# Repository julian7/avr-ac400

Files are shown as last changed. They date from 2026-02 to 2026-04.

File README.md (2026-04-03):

# Record Power AC400 controller

This repository contains a drop-in replacement PCB and firmware for the [Record Power AC400 Air Filter controller](https://www.recordpower.co.uk/product/two-stage-air-filter-with-remote-3-speeds-and-time-delay).

The original AC400 controller is prone to failure due to its simplistic power supply design, which often results in various failures. While the company's support is very good, the replacement controller is still prone to the same issues.

This design aims to provide a solution that is more robust, and tries to keep using original parts where possible. It also uses an ~~ATmega88PA~~ ATmega328P microcontroller, as existing refurbishment stock (note: the ATmega88 I had probably has SPIEN fuse unprogrammed, so I couldn't flash it at the end). The PCB and firmware is compatible with the whole line of ATmega48P/88P/168PA/328P line though.

## Case design

The board PCB is designed to fit into the original AC400 electronics enclosure, but there is a different LED divider grill design, which is 3D printed. The 3D model and the FreeCAD source are available in the `mechanical` directory, and it can be printed with a 3D printer.

The 3D design and model for the case is also provided, to allow further modifications.

## PCB design

The PCB is designed using KiCad 10, and is available in the `hardware` directory. The form factor is designed to fit into the original AC400 enclosure, and it uses the same connectors for the fan and power supply. It relies of the Alternative Kicad Library plugin for resistor footprints. Interactive BOM is generated using the [Interactive Html Bom](Github: https://github.com/openscopeproject/InteractiveHtmlBom) plugin, and gerber file packages are generated using the [gerber to order](https://github.com/asukiaaa/gerber_to_order) plugin.

## Firmware

The firmware is written in C using AVR-GCC toolchain, and it is available in the `firmware` directory. It is based on the original firmware functionality, with some improvements and bug fixes.

## Flashing the firmware

To flash the firmware onto the microcontroller, you will need an AVR programmer (e.g., USBasp, [ATMEL-ICE](https://www.microchip.com/en-us/development-tool/atatmel-ice)) and AVRDUDE software.

## Measurement points and troubleshooting

The PCB includes test points for measuring various signals:

- TP1: 3.3V power supply
- TP2: Ground
- TP3: Low speed mosfet drain
- TP4: Low speed mosfet gate
- TP5: Mid speed mosfet drain
- TP6: Mid speed mosfet gate
- TP7: High speed mosfet drain
- TP8: High speed mosfet gate

When troubleshooting, supply 3.3V power to the PCB through J8, so that 230V is not present on the board.

J1 is providing standard ISP connectivity. Manual reset can be performed by shorting JP1 (also labeled "RESET").

## Wiring and functions

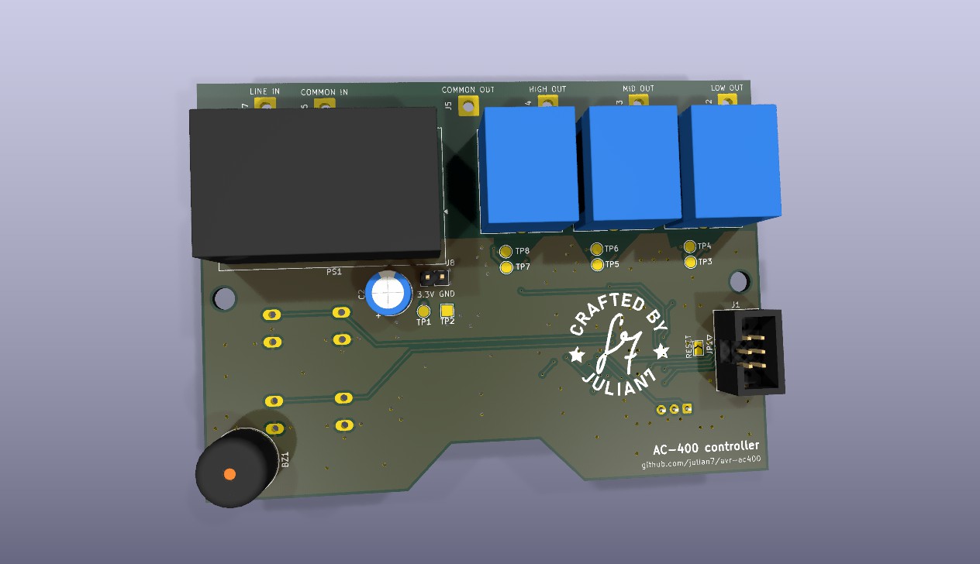
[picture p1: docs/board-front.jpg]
Board front


When assembled into the original AC400 enclosure, the PCB will be connected to the following components:

- LINE IN: 230V AC input
- COMMON IN: Common line for the fan and the power supply
- COMMON OUT: White wire to the fan
- LOW OUT: Blue (or brown) wire to the fan
- MID OUT: Black wire to the fan
- HIGH OUT: Red wire to the fan

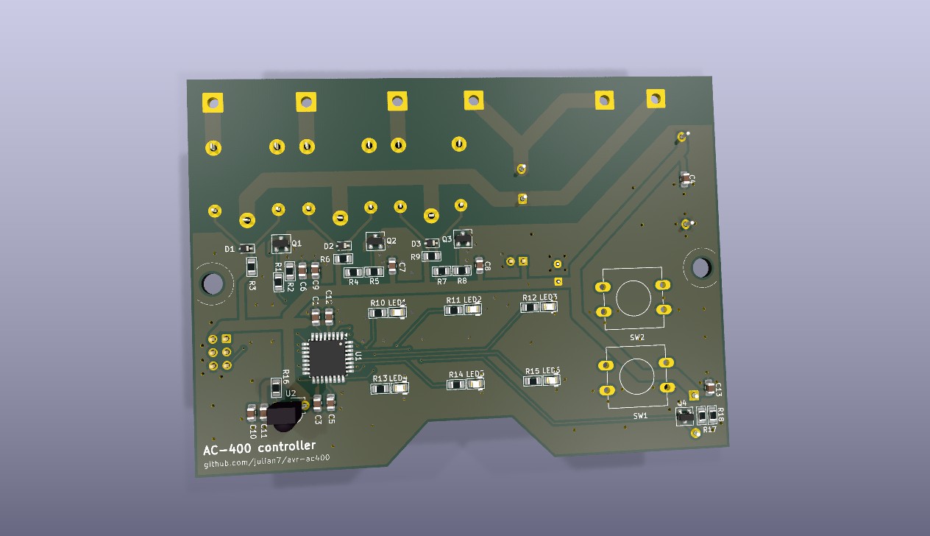
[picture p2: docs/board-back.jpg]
Board back


LED functions:

- LED1: Timer for 1 hour
- LED2: Timer for 2 hours
- LED3: Timer for 4 hours
- LED4: High speed indicator
- LED5: Medium speed indicator
- LED6: Low speed indicator

Button functions:

- SW1: On/Speed (cycles through Off, Low, Mid, High)
- SW2: Off

Infrared remote control functions:

- Red: Off
- Green: On/Speed
- Yellow: Timer (cycles through Off, 1 hour, 2 hours, 4 hours)

Buzzer signals:

- Short beep: Button press / infrared button feedback
- Long beep: Timer end
- Long beep with 1/2/4 short beeps: timer set to 1/2/4 hours
- Two long beeps: Off

## Build experience

Building this project was quite an experience. First off, soldering the MCU was not much of a challenge, and I felt like I could handle 0603 package size too, or even 0402 if the space is tight. I would use an ESP32-C3 board if I were to do it again: that would make it remote controllable.

Originally, I wanted to use an old ATmega88PA, but I couldn't even read its fuses. So that I ordered a few ATmega328P, which are pin-compatible. Fortunately, because I could made one of them a short circuit. It would've been nicer if the design accepted ATmega328PB, but I just didn't want to risk cutting wires at that point.

I almost fried my Raspberry Pi4 while writing the firmware, so buying a very cheap USBASP now feels like a no brainer. It's also not that bad if you don't screw up the ISP pinout. Fortunately, I could patch it up with bodge wires. Also, there was a nasty case of weird behavior and browning out, but as it turns out that was just microzig acting up. Switching back to avr-libc made the issue go away.

The original plan was to reuse the original case and the 12mm TACT switches, but I mistakenly ordered an earlier version of the PCB, where mounting holes have been placed closer together so I ended up 3D printing my own case. Later on, I even managed to break off the buttons as I tried to assemble it back together, and I only had 6x6mm switches so I ended up propping up some button spacers to be able to operate the device.

All in all, I'm very happy about the outcome.  Obviously it could've been much better, but this is still well beyond my expectations.

## Similar projects

- [AC400Controller](https://github.com/thikone/AC400Controller): drop-in replacement PCB, firmware, and 3D printed enclosure. It uses Arduino Nano as the controller.

## License

This project is licensed under the Creative Commons Attribution 4.0 International License. See the [LICENSE](./LICENSE.md) file for details.

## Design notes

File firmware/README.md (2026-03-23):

# Firmware for the AC400 controller

## Install toolchain

- Install [just](https://github.com/casey/just/releases)
- Install the [AVR Libc](https://avrdudes.github.io/avr-libc/) toolchain. For exmple, on Debian / Ubuntu:

```shell
sudo apt update
sudo apt install -y gcc-avr binutils-avr avr-libc avrdude
```

On MacOS, you can use Homebrew:

```shell
brew install avr-gcc avrdude
```

## Build and flash

Run

```shell
make
just flash
```

The flash utility is taking a few parameters to specify your environment. The default values are for a Raspberry Pi using SPI0 from its GPIO, but you can override them with environment variables. For example:

- AVR_PROGRAMMER: The programmer to use with `avrdude`. Default is `usbasp-clone`.
- AVR_PART: The AVR part number to flash. Default is `m328p`.
- AVR_PORT: The port to use for flashing. Default is empty.
- AVR_FREQ: The frequency for flashing. Default is empty.
- TARGET: The target to flash. Default is `ac400`. This will flash `ac400.hex`.

Run `sudo -E just flash` if you need root permissions to access the SPI device. You can also set up udev rules to allow non-root access to the SPI device.

Please note: `-E` is used to preserve the environment variables when running `just` with `sudo`.

## Setting Fuses

Sometimes, you may need to set the fuses on the AVR microcontroller to configure its behavior. Setting and reading fuses are easy with just recipes:

```shell
just read-fuses
```

```shell
just set-fuses [-l 0xLF] [-h 0xHF] [-e 0xEF]
```

Where:
- `-l`: Set the low fuse byte (default: 0xe2).
- `-h`: Set the high fuse byte (default: 0xdf).
- `-e`: Set the extended fuse byte (default: 0xff).

## Default fuse settings

- LFUSE: establish clock source (CKDIV8 = 1, CKOUT = 1, SUT = 10, CKSEL = 0010). To measure clock, set CKOUT fuse (so that LFUSE should be 0xa2).
- HFUSE: RSTDISBL = 1, DWEN = 1, SPIEN = 0, WDTON = 1, EESAVE = 1, BOOTSZ = 11, BOOTRST = 1
- EFUSE: BODLEVEL = 111 (Brown-out detection disabled)

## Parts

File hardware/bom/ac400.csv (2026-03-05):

Reference | Qty | Value | DNP | Exclude from BOM | Exclude from Board | Footprint | Datasheet | Manufacturer | Distributor Link 1 | Distributor Link 2 | Distributor Link 3
BZ1 | 1 | Buzzer |  |  |  | Buzzer_Beeper:Buzzer_12x9.5RM7.6 | ~
C1,C3,C5,C6,C7,C8,C10,C12,C13 | 9 | 100n |  |  |  | Capacitor_SMD:C_0805_2012Metric_Pad1.18x1.45mm_HandSolder | ~
C2 | 1 | 470u |  |  |  | Capacitor_THT:CP_Radial_D8.0mm_P3.50mm | ~
C4,C9,C11 | 3 | 10u |  |  |  | Capacitor_SMD:C_0805_2012Metric_Pad1.18x1.45mm_HandSolder | ~
D1,D2,D3 | 3 | 1N4007 |  |  |  | Diode_SMD:D_SOD-323 | https://www.tme.eu/Document/5f8ffc5ac30fc86bac97d66040bf5502/1n400x.pdf
J1 | 1 | AVR-ISP-10 |  |  |  | Connector_IDC:IDC-Header_2x05_P2.54mm_Vertical | ~
J2 | 1 | LOW OUT |  | Excluded from BOM |  | Connector_Wire:SolderWire-1.5sqmm_1x01_D1.7mm_OD3.9mm | ~
J3 | 1 | MID OUT |  | Excluded from BOM |  | Connector_Wire:SolderWire-1.5sqmm_1x01_D1.7mm_OD3.9mm | ~
J4 | 1 | HIGH OUT |  | Excluded from BOM |  | Connector_Wire:SolderWire-1.5sqmm_1x01_D1.7mm_OD3.9mm | ~
J5 | 1 | COMMON OUT |  | Excluded from BOM |  | Connector_Wire:SolderWire-1.5sqmm_1x01_D1.7mm_OD3.9mm | ~
J6 | 1 | COMMON IN |  | Excluded from BOM |  | Connector_Wire:SolderWire-1.5sqmm_1x01_D1.7mm_OD3.9mm | ~
J7 | 1 | LINE IN |  | Excluded from BOM |  | Connector_Wire:SolderWire-1.5sqmm_1x01_D1.7mm_OD3.9mm | ~
J8 | 1 | 3.3V IN |  |  |  | Connector_PinHeader_2.54mm:PinHeader_1x02_P2.54mm_Vertical | ~
JP1 | 1 | Reset |  | Excluded from BOM |  | Jumper:SolderJumper-2_P1.3mm_Open_TrianglePad1.0x1.5mm | ~
K1,K2,K3 | 3 | SRD-03VDC-SL-C |  |  |  | Relay_THT:Relay_SPDT_SANYOU_SRD_Series_Form_C | http://www.sanyourelay.ca/public/products/pdf/SRD.pdf | Songle | https://www.hestore.hu/prod_10049169.html
LED1,LED2,LED3,LED4,LED5,LED6 | 6 | OF-SMD 2012 Green |  |  |  | PCM_LED_SMD_AKL:LED_0805_2012Metric | ~ | OPTOFLASH | https://www.hestore.hu/prod_10025832.html
PS1 | 1 | HLK-5M03 |  |  |  | Converter_ACDC:Converter_ACDC_Hi-Link_HLK-5Mxx | http://h.hlktech.com/download/ACDC%E7%94%B5%E6%BA%90%E6%A8%A1%E5%9D%975W%E7%B3%BB%E5%88%97/1/%E6%B5%B7%E5%87%8C%E7%A7%915W%E7%B3%BB%E5%88%97%E7%94%B5%E6%BA%90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
Q1,Q2,Q3,Q4 | 4 | IRLML2502 |  |  |  | PCM_Package_TO_SOT_SMD_AKL:SOT-23 | https://www.tme.eu/Document/48a23309a6589a98e2dca6345156a95a/IRLML2502TRPBF.pdf
R1,R4,R7,R17 | 4 | 100 |  |  |  | PCM_Resistor_SMD_AKL:R_0805_2012Metric_Pad1.15x1.40mm_HandSolder | ~
R2,R5,R8,R18 | 4 | 100k |  |  |  | PCM_Resistor_SMD_AKL:R_0805_2012Metric_Pad1.15x1.40mm_HandSolder | ~
R3,R6,R9 | 3 | 2.2 |  |  |  | PCM_Resistor_SMD_AKL:R_0805_2012Metric_Pad1.15x1.40mm_HandSolder | ~
R10,R11,R12,R13,R14,R15 | 6 | 120 |  |  |  | PCM_Resistor_SMD_AKL:R_0805_2012Metric_Pad1.15x1.40mm_HandSolder | ~
R16 | 1 | 10k |  |  |  | PCM_Resistor_SMD_AKL:R_0805_2012Metric_Pad1.15x1.40mm_HandSolder | ~
SW1 | 1 | ON |  |  |  | Button_Switch_THT:SW_PUSH-12mm | ~
SW2 | 1 | OFF |  |  |  | Button_Switch_THT:SW_PUSH-12mm | ~
SYM1 | 1 | Board footprint |  | Excluded from BOM |  | ac400:board_shape | ~
SYM2 | 1 | Julian7 logo |  | Excluded from BOM |  | ac400:julian7_makers_mark | ~
TP1 | 1 | 3.3V |  | Excluded from BOM |  | TestPoint:TestPoint_Pad_D2.0mm | ~
TP2 | 1 | GND |  | Excluded from BOM |  | TestPoint:TestPoint_Pad_2.0x2.0mm | ~
TP3 | 1 | LD |  | Excluded from BOM |  | TestPoint:TestPoint_Pad_D2.0mm | ~
TP4 | 1 | LG |  | Excluded from BOM |  | TestPoint:TestPoint_Pad_D2.0mm | ~
TP5 | 1 | MD |  | Excluded from BOM |  | TestPoint:TestPoint_Pad_D2.0mm | ~
TP6 | 1 | MG |  | Excluded from BOM |  | TestPoint:TestPoint_Pad_D2.0mm | ~
TP7 | 1 | HD |  | Excluded from BOM |  | TestPoint:TestPoint_Pad_D2.0mm | ~
TP8 | 1 | HG |  | Excluded from BOM |  | TestPoint:TestPoint_Pad_D2.0mm | ~
U1 | 1 | ATmega88PA-A |  |  |  | Package_QFP:TQFP-32_7x7mm_P0.8mm | https://www.microchip.com/en-us/product/ATmega88PA | Microchip Technology | https://www.digikey.hu/hu/products/detail/microchip-technology/ATMEGA88PA-AU/1886228 | https://hu.mouser.com/ProductDetail/Microchip-Technology/ATMEGA88PA-AU?qs=VXy%252BgAb0zZQ5AzLsp2xy0A%3D%3D | https://www.hestore.hu/prod_10029337.html
U2 | 1 | TSOP38238 |  |  |  | OptoDevice:Vishay_MINICAST-3Pin | http://www.vishay.com/docs/82491/tsop382.pdf

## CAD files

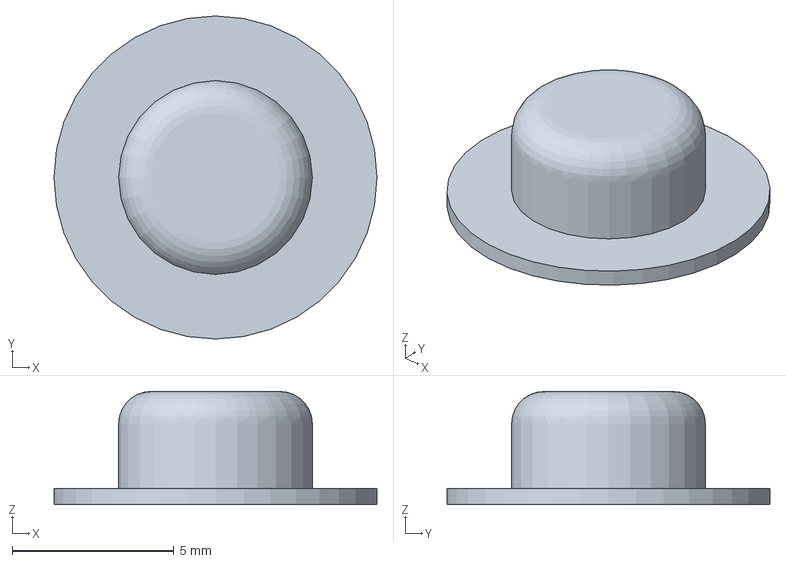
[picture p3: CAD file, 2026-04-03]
mechanical/ac400board-button.3mf
10.0 x 10.0 x 3.50 mm

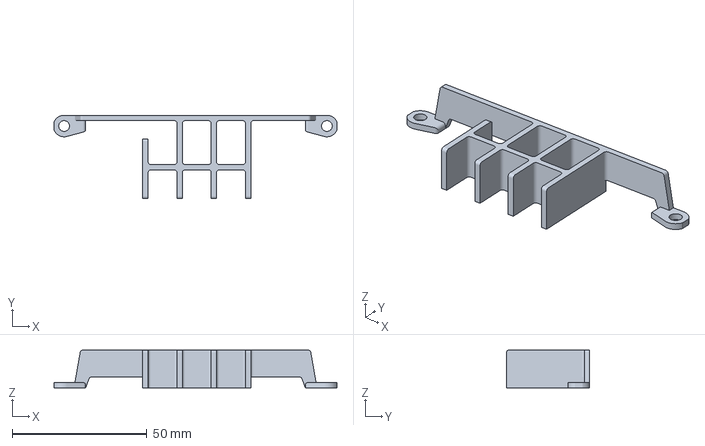
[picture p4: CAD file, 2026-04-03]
mechanical/ac400board-divider.3mf
105.0 x 31.0 x 14.0 mm

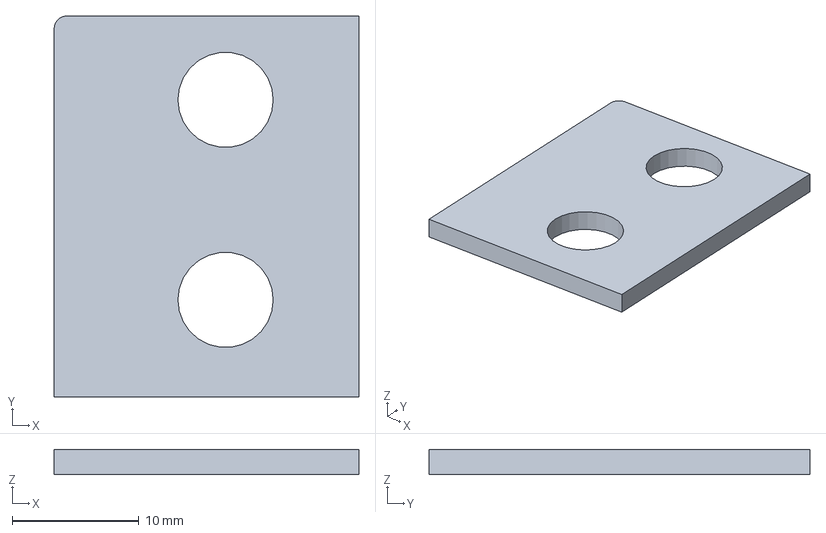
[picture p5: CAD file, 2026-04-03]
mechanical/ac400board-switch-stabilizer.3mf
24.0 x 30.0 x 2.00 mm

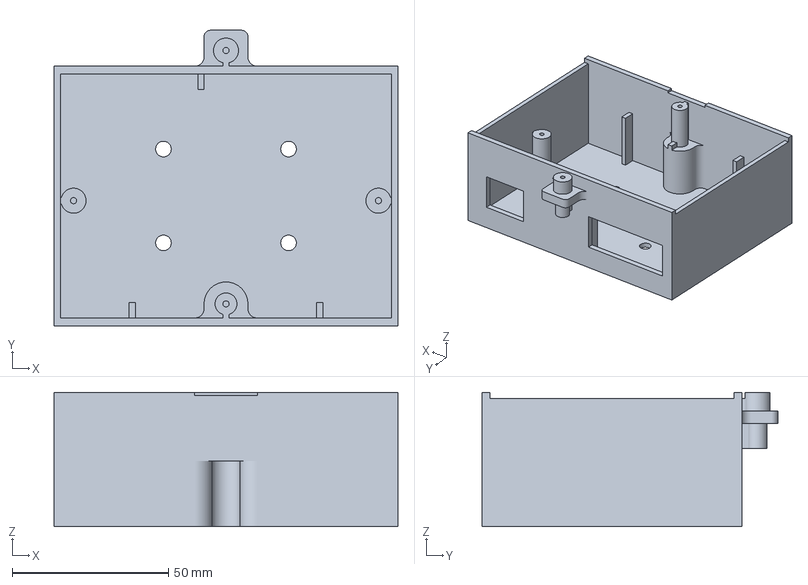
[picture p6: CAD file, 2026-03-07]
mechanical/ac400board-box.3mf
110.0 x 94.5 x 43.0 mm

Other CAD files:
mechanical/ac400board.FCStd

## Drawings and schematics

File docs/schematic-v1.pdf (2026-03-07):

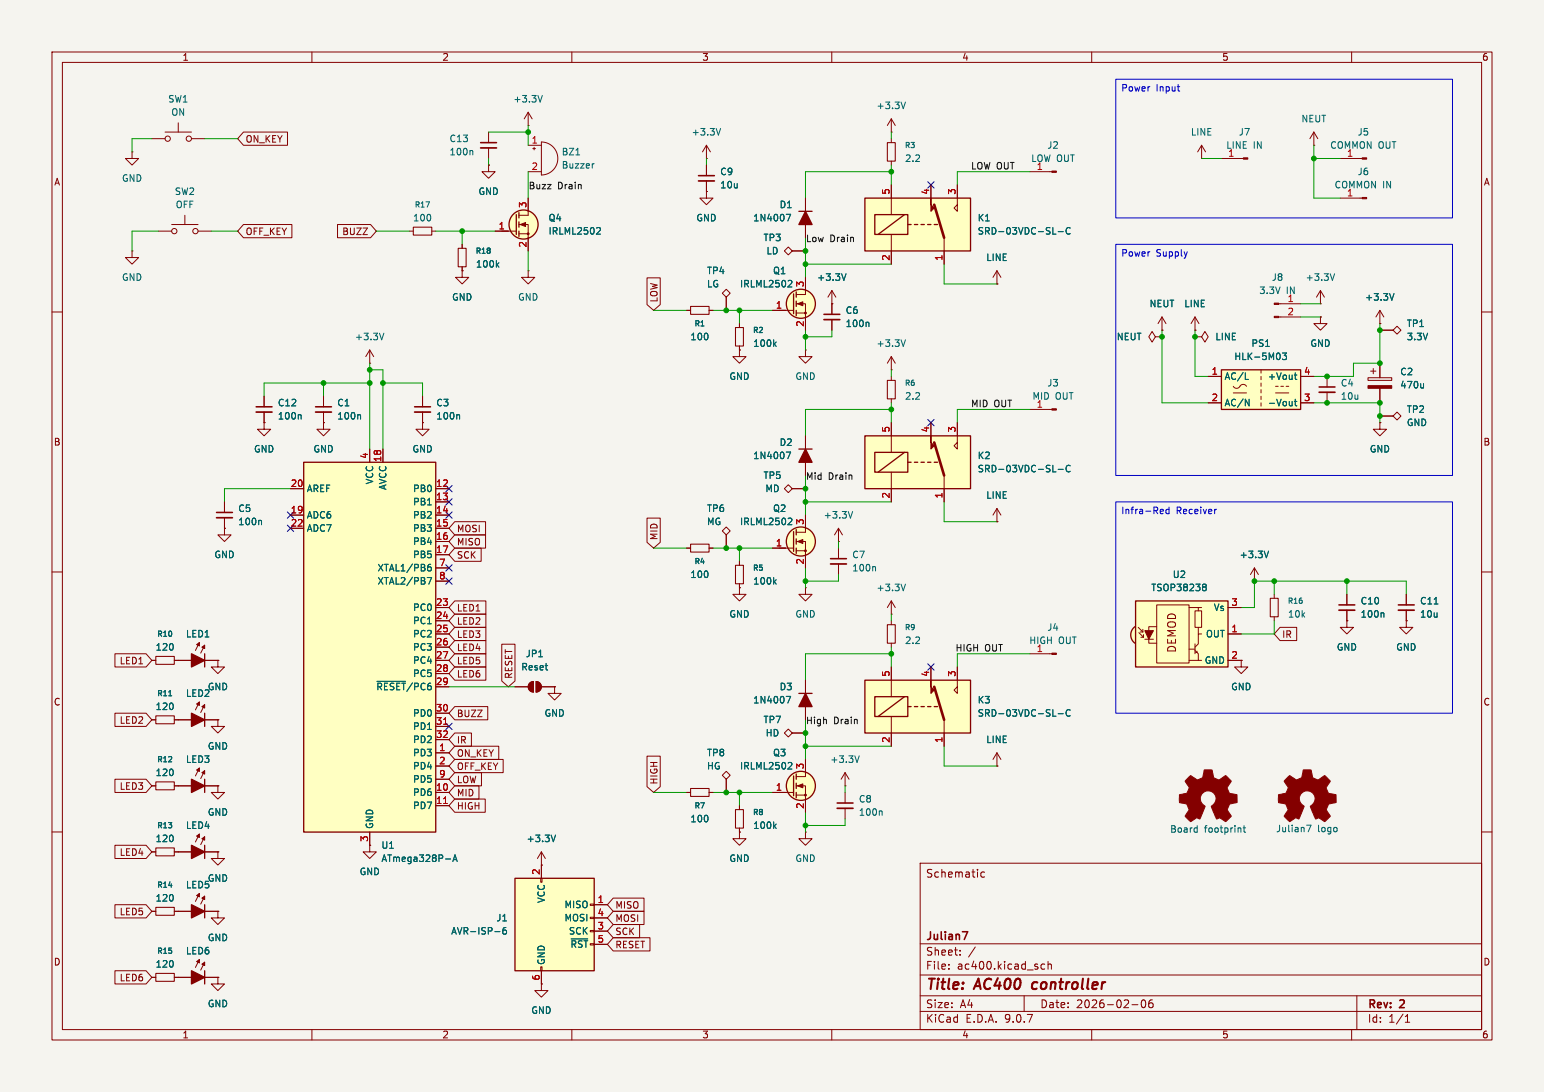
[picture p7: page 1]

J5 COMMON OUT GND
LOW OUT MID OUT Mid Drain

6 MISO 1 MOSI 4 SCK 3 ~{RST}5 +3.3V GND GND
LED4
LED5 R13 120

Id: 1/1 Title: AC400 controller File: ac400.kicad_sch Sheet: / Julian7 Schematic

6 MISO 1 MOSI 4 SCK 3 ~{RST}5

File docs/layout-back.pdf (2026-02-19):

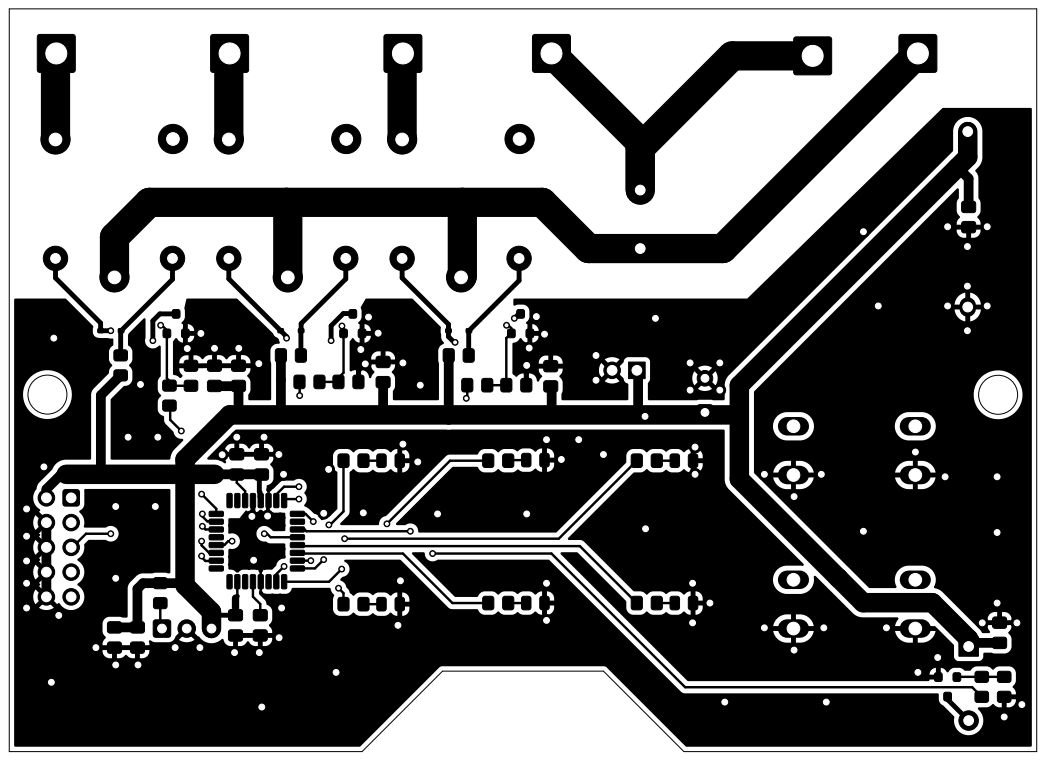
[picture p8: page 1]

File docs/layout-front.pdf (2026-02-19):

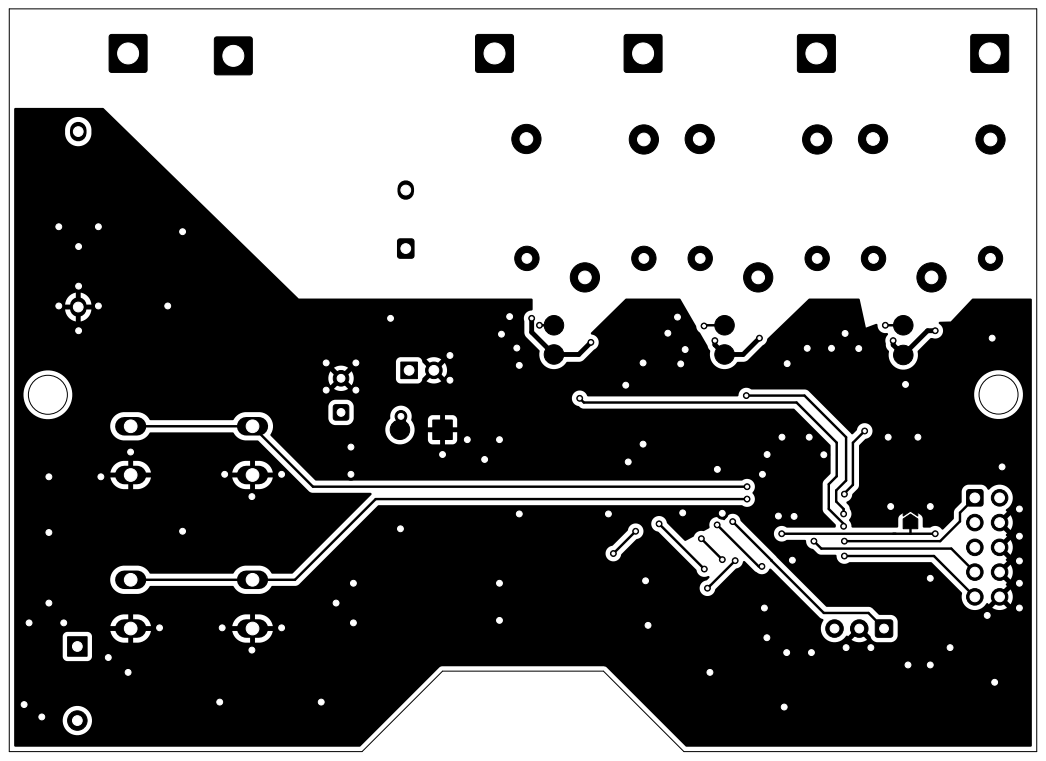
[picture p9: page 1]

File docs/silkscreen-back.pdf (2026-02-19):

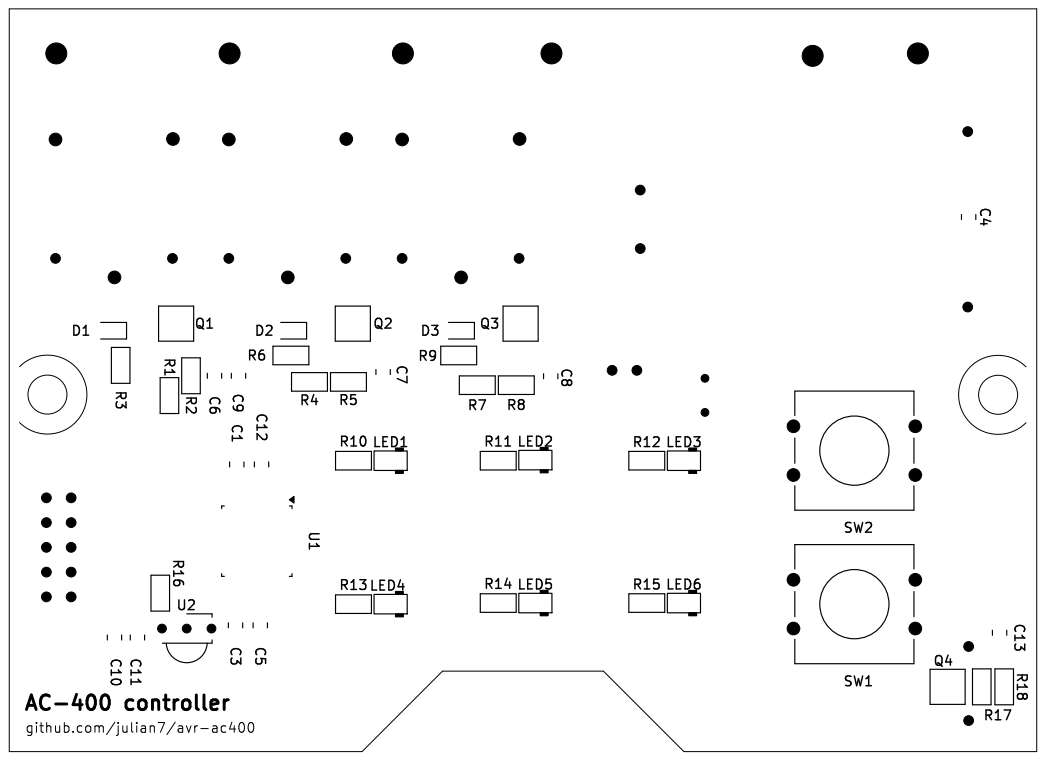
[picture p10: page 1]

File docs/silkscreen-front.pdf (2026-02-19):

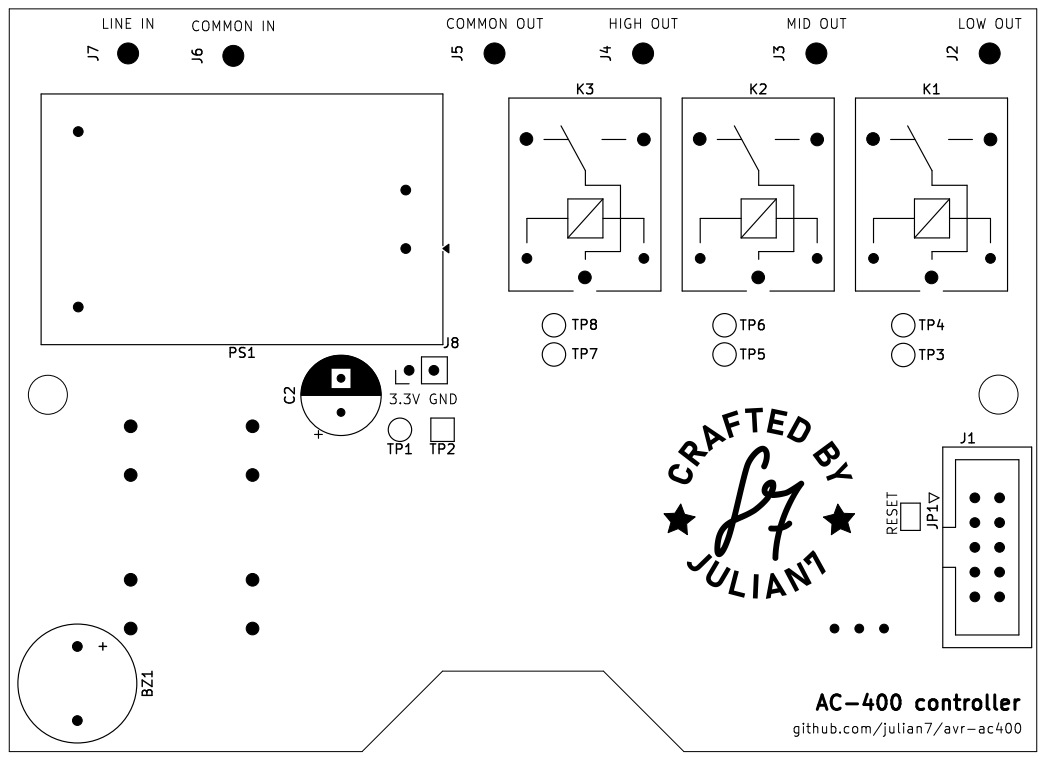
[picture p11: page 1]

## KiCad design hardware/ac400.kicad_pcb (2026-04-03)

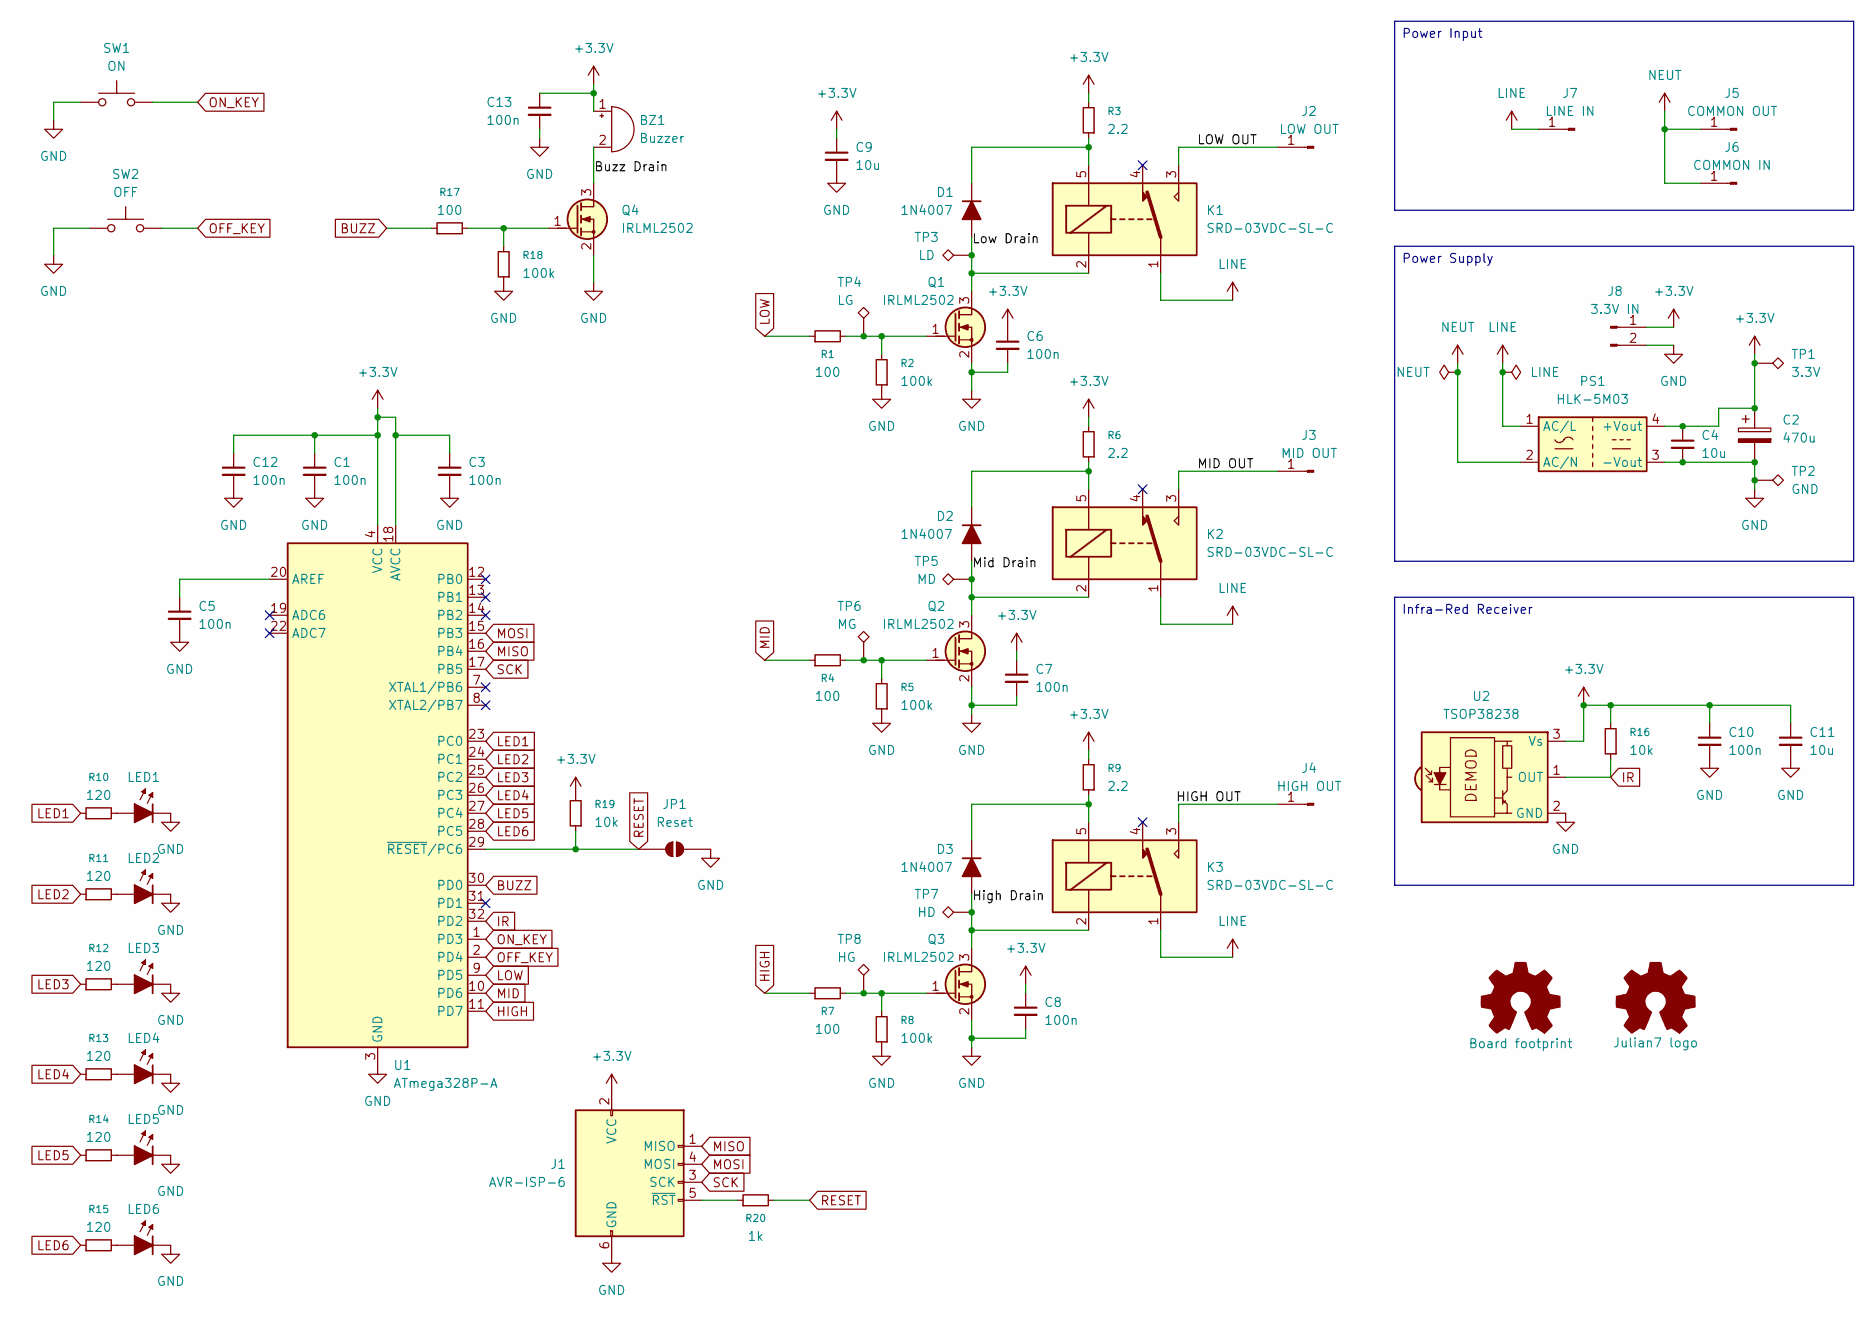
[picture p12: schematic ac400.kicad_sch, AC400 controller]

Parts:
BZ1: Buzzer; Buzzer_12x9.5RM7.6
C1, C3, C5, C6, C7, C8, C10, C12, C13: 100n; C_0805_2012Metric_Pad1.18x1.45mm_HandSolder
C2: 470u; CP_Radial_D8.0mm_P3.50mm
C4, C9, C11: 10u; C_0805_2012Metric_Pad1.18x1.45mm_HandSolder
D1, D2, D3: 1N4007; D_SOD-323
J1: AVR-ISP-6; IDC-Header_2x03_P2.54mm_Vertical
J2: LOW OUT; SolderWire-1.5sqmm_1x01_D1.7mm_OD3.9mm
J3: MID OUT; SolderWire-1.5sqmm_1x01_D1.7mm_OD3.9mm
J4: HIGH OUT; SolderWire-1.5sqmm_1x01_D1.7mm_OD3.9mm
J5: COMMON OUT; SolderWire-1.5sqmm_1x01_D1.7mm_OD3.9mm
J6: COMMON IN; SolderWire-1.5sqmm_1x01_D1.7mm_OD3.9mm
J7: LINE IN; SolderWire-1.5sqmm_1x01_D1.7mm_OD3.9mm
J8: 3.3V IN; PinHeader_1x02_P2.54mm_Vertical
JP1: Reset; SolderJumper-2_P1.3mm_Open_TrianglePad1.0x1.5mm
K1, K2, K3: SRD-03VDC-SL-C; Relay_SPDT_SANYOU_SRD_Series_Form_C
LED1, LED2, LED3, LED4, LED5, LED6: OF-SMD 2012 Green; LED_0805_2012Metric
PS1: HLK-5M03; Converter_ACDC_Hi-Link_HLK-5Mxx
Q1, Q2, Q3, Q4: IRLML2502; SOT-23
R1, R4, R7, R17: 100; R_0805_2012Metric_Pad1.15x1.40mm_HandSolder
R2, R5, R8, R18: 100k; R_0805_2012Metric_Pad1.15x1.40mm_HandSolder
R3, R6, R9: 2.2; R_0805_2012Metric_Pad1.15x1.40mm_HandSolder
R10, R11, R12, R13, R14, R15: 120; R_0805_2012Metric_Pad1.15x1.40mm_HandSolder
R16, R19: 10k; R_0805_2012Metric_Pad1.15x1.40mm_HandSolder
R20: 1k; R_0805_2012Metric_Pad1.15x1.40mm_HandSolder
SW1: ON; SW_PUSH-12mm
SW2: OFF; SW_PUSH-12mm
SYM1: Board footprint; board_shape
SYM2: Julian7 logo; julian7_makers_mark
TP1: 3.3V; TestPoint_Pad_D2.0mm
TP2: GND; TestPoint_Pad_2.0x2.0mm
TP3: LD; TestPoint_Pad_D2.0mm
TP4: LG; TestPoint_Pad_D2.0mm
TP5: MD; TestPoint_Pad_D2.0mm
TP6: MG; TestPoint_Pad_D2.0mm
TP7: HD; TestPoint_Pad_D2.0mm
TP8: HG; TestPoint_Pad_D2.0mm
U1: ATmega328P-A; TQFP-32_7x7mm_P0.8mm
U2: TSOP38238; Vishay_MINICAST-3Pin

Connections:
+3.3V: BZ1.1 (+), C1.1, C2.1, C3.1, C4.1, C6.1, C7.1, C8.1, C9.1, C10.1, C11.1, C12.1, C13.1, J1.2 (VCC), J8.1, PS1.4 (+Vout), R3.2, R6.2, R9.2, R16.2, R19.2, TP1.1 (1_1), U1.4 (VCC), U1.6 (VCC), U1.18 (AVCC), U2.3 (Vs)
/Buzz Drain: BZ1.2 (-), Q4.3 (D)
/HIGH OUT: J4.1 (Pin_1_1), K3.3
/High Drain: D3.2 (A), K3.2, Q3.3 (D), TP7.1 (1_1)
/LOW OUT: J2.1 (Pin_1_1), K1.3
/Low Drain: D1.2 (A), K1.2, Q1.3 (D), TP3.1 (1_1)
/MID OUT: J3.1 (Pin_1_1), K2.3
/Mid Drain: D2.2 (A), K2.2, Q2.3 (D), TP5.1 (1_1)
BUZZ: R17.1, U1.30 (PD0)
GND: C1.2, C2.2, C3.2, C4.2, C5.2, C6.2, C7.2, C8.2, C9.2, C10.2, C11.2, C12.2, C13.2, J1.6 (GND), J8.2, JP1.2 (B), LED1.1 (K), LED2.1 (K), LED3.1 (K), LED4.1 (K), LED5.1 (K), LED6.1 (K), PS1.3 (-Vout), Q1.2 (S), Q2.2 (S), Q3.2 (S), Q4.2 (S), R2.1, R5.1, R8.1, R18.1, SW1.1, SW2.1, TP2.1 (1_1), U1.3 (GND), U1.5 (GND), U1.21 (GND), U2.2 (GND)
HIGH: R7.1, U1.11 (PD7)
IR: R16.1, U1.32 (PD2), U2.1 (OUT)
LED1: R10.1, U1.23 (PC0)
LED2: R11.1, U1.24 (PC1)
LED3: R12.1, U1.25 (PC2)
LED4: R13.1, U1.26 (PC3)
LED5: R14.1, U1.27 (PC4)
LED6: R15.1, U1.28 (PC5)
LINE: J7.1 (Pin_1_1), K1.1, K2.1, K3.1, PS1.1 (AC/L)
LOW: R1.1, U1.9 (PD5)
MID: R4.1, U1.10 (PD6)
MISO: J1.1 (MISO), U1.16 (PB4)
MOSI: J1.4 (MOSI), U1.15 (PB3)
NEUT: J5.1 (Pin_1_1), J6.1 (Pin_1_1), PS1.2 (AC/N)
unnamed: D1.1 (K), K1.5, R3.1
unnamed: D2.1 (K), K2.5, R6.1
unnamed: D3.1 (K), K3.5, R9.1
unnamed: J1.5 (~RST), R20.1
unnamed: LED1.2 (A), R10.2
unnamed: LED2.2 (A), R11.2
unnamed: LED3.2 (A), R12.2
unnamed: LED4.2 (A), R13.2
unnamed: LED5.2 (A), R14.2
unnamed: LED6.2 (A), R15.2
unnamed: Q1.1 (G), R1.2, R2.2, TP4.1 (1_1)
unnamed: Q2.1 (G), R4.2, R5.2, TP6.1 (1_1)
unnamed: Q3.1 (G), R7.2, R8.2, TP8.1 (1_1)
unnamed: Q4.1 (G), R17.2, R18.2
unnamed: C5.1, U1.20 (AREF)
OFF_KEY: SW2.2, U1.2 (PD4)
ON_KEY: SW1.2, U1.1 (PD3)
RESET: JP1.1 (A), R19.1, R20.2, U1.29 (~RESET/PC6)
SCK: J1.3 (SCK), U1.17 (PB5)

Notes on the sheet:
Power Input
Power Supply
Infra-Red Receiver

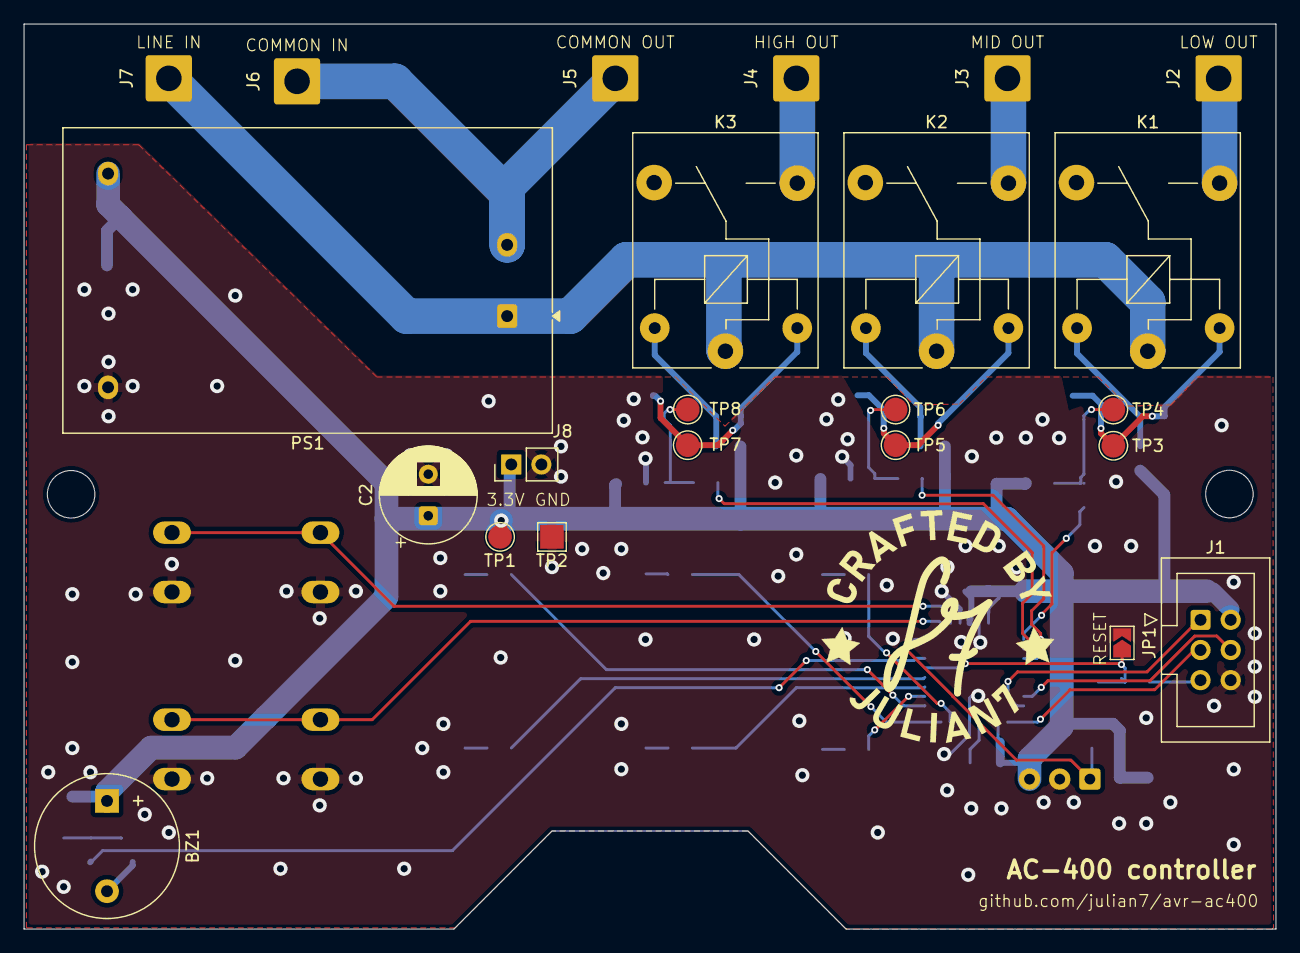
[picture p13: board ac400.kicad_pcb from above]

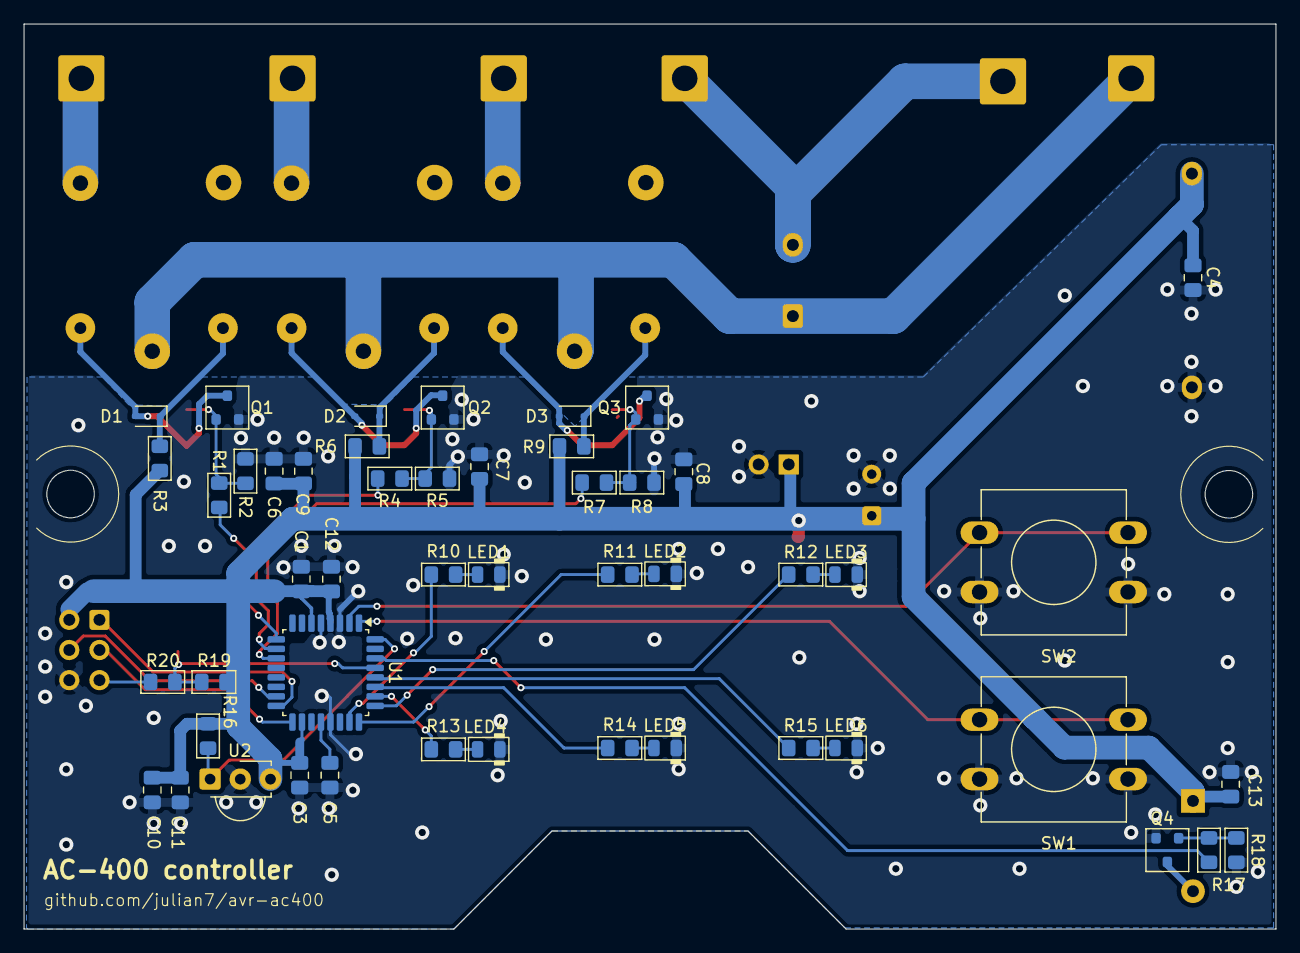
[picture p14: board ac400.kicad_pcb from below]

Board: 2 copper layers, 105.4 x 76.2 mm, 74 parts (49 on the bottom side), 43 nets.

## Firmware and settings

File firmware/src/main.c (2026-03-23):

#include <avr/interrupt.h>
#include <avr/io.h>
#include <stdbool.h>
#include <stdint.h>

#include "config.h"
#include "gpio.h"
#include "ir.h"

/*
 * AC400 firmware:
 * - Relays: active-high
 * - Buttons: active-low with internal pullups
 */

#define BUZZER_SHORT_MS 80
#define BUZZER_LONG_MS 400
#define BUZZER_GAP_MS 120

/* Timer0: 1ms system tick */
#define TIMER0_PRESCALE 64UL
#define TIMER0_OCR ((F_CPU / TIMER0_PRESCALE / 1000UL) - 1U)

#define IR_CMD_ON 0x30
#define IR_CMD_OFF 0x90
#define IR_CMD_TIME 0xA0

typedef enum { SPEED_OFF = 0, SPEED_LOW, SPEED_MID, SPEED_HIGH } speed_t;

typedef struct {
  uint8_t integrator;
  bool pressed;
} debounce_t;

static volatile uint32_t g_ms = 0;

static speed_t g_speed = SPEED_OFF;
static uint8_t g_timer_sel_hours = 0; /* 0,1,2,4 */
static uint32_t g_timer_seconds_remaining = 0;

static uint32_t g_buzzer_next_ms = 0;
static uint8_t g_buzzer_state = 0;
static uint8_t g_buzzer_beeps_remaining = 0;
static uint16_t g_buzzer_on_ms = 0;
static uint16_t g_buzzer_off_ms = 0;
static uint8_t g_buzzer_followup_shorts = 0;

static void buzzer_set(uint8_t on) { gpio_write(BUZZER_PIN, on ? 1 : 0); }

static void buzzer_start(uint8_t beeps, uint16_t on_ms, uint16_t off_ms) {
  if (beeps == 0)
    return;
  uint32_t now_ms;
  uint8_t sreg = SREG;
  cli();
  now_ms = g_ms;
  SREG = sreg;

  g_buzzer_followup_shorts = 0;
  g_buzzer_beeps_remaining = beeps;
  g_buzzer_on_ms = on_ms;
  g_buzzer_off_ms = off_ms;
  g_buzzer_state = 1;
  buzzer_set(1);
  g_buzzer_next_ms = now_ms + on_ms;
}

static void buzzer_start_timer(uint8_t shorts) {
  if (shorts == 0)
    return;
  buzzer_start(1, BUZZER_LONG_MS, BUZZER_GAP_MS);
  g_buzzer_followup_shorts = shorts;
}

static void buzzer_update(uint32_t now_ms) {
  if (g_buzzer_state == 0)
    return;
  if ((int32_t)(now_ms - g_buzzer_next_ms) < 0)
    return;

  if (g_buzzer_state == 1) {
    buzzer_set(0);
    g_buzzer_state = 2;
    g_buzzer_next_ms = now_ms + g_buzzer_off_ms;
  } else {
    if (g_buzzer_beeps_remaining > 1) {
      g_buzzer_beeps_remaining--;
      g_buzzer_state = 1;
      buzzer_set(1);
      g_buzzer_next_ms = now_ms + g_buzzer_on_ms;
    } else {
      g_buzzer_state = 0;
      g_buzzer_beeps_remaining = 0;
      if (g_buzzer_followup_shorts > 0) {
        uint8_t shorts = g_buzzer_followup_shorts;
        g_buzzer_followup_shorts = 0;
        buzzer_start(shorts, BUZZER_SHORT_MS, BUZZER_GAP_MS);
      }
    }
  }
}

static void update_leds(void) {
  gpio_write(LED1_PIN, g_timer_sel_hours == 1);
  gpio_write(LED2_PIN, g_timer_sel_hours == 2);
  gpio_write(LED3_PIN, g_timer_sel_hours == 4);

  gpio_write(LED4_PIN, g_speed == SPEED_HIGH);
  gpio_write(LED5_PIN, g_speed == SPEED_MID);
  gpio_write(LED6_PIN, g_speed == SPEED_LOW);
}

static void relays_all_off(void) {
  gpio_write(RELAY_LOW_PIN, 0);
  gpio_write(RELAY_MID_PIN, 0);
  gpio_write(RELAY_HIGH_PIN, 0);
}

static void set_speed(speed_t speed) {
  relays_all_off();
  g_speed = speed;
  if (speed == SPEED_LOW) {
    gpio_write(RELAY_LOW_PIN, 1);
  } else if (speed == SPEED_MID) {
    gpio_write(RELAY_MID_PIN, 1);
  } else if (speed == SPEED_HIGH) {
    gpio_write(RELAY_HIGH_PIN, 1);
  }
  update_leds();
}

static speed_t next_speed(speed_t s) {
  switch (s) {
  case SPEED_OFF:
    return SPEED_LOW;
  case SPEED_LOW:
    return SPEED_MID;
  case SPEED_MID:
    return SPEED_HIGH;
  default:
    return SPEED_LOW;
  }
}

static uint8_t next_timer_sel_hours(uint8_t h) {
  switch (h) {
  case 0:
    return 1;
  case 1:
    return 2;
  case 2:
    return 4;
  default:
    return 0;
  }
}

static void rotate_timer(void) {
  g_timer_sel_hours = next_timer_sel_hours(g_timer_sel_hours);

  if (g_timer_sel_hours == 0) {
    g_timer_seconds_remaining = 0;
  } else {
    g_timer_seconds_remaining = (uint32_t)g_timer_sel_hours * 3600UL;
  }

  if (g_timer_sel_hours > 0) {
    buzzer_start_timer(g_timer_sel_hours);
  }

  update_leds();
}

static bool debounce_update(debounce_t *db, bool raw_pressed) {
  const uint8_t max = 3;
  if (raw_pressed) {
    if (db->integrator < max)
      db->integrator++;
  } else {
    if (db->integrator > 0)
      db->integrator--;
  }

  bool new_pressed = (db->integrator >= max);
  bool pressed_event = (!db->pressed && new_pressed);
  db->pressed = new_pressed;
  return pressed_event;
}

static void io_init(void) {
  gpio_set_output(RELAY_LOW_PIN);
  gpio_set_output(RELAY_MID_PIN);
  gpio_set_output(RELAY_HIGH_PIN);
  relays_all_off();

  gpio_set_output(BUZZER_PIN);
  buzzer_set(0);

  gpio_set_input(ON_KEY_PIN, 1);
  gpio_set_input(OFF_KEY_PIN, 1);

  gpio_set_output(LED1_PIN);
  gpio_set_output(LED2_PIN);
  gpio_set_output(LED3_PIN);
  gpio_set_output(LED4_PIN);
  gpio_set_output(LED5_PIN);
  gpio_set_output(LED6_PIN);
  update_leds();
}

static void timer0_init(void) {
  TCCR0A = (1 << WGM01);
  TCCR0B = (1 << CS01) | (1 << CS00);
  OCR0A = (uint8_t)TIMER0_OCR;
  TIMSK0 = (1 << OCIE0A);
}

ISR(TIMER0_COMPA_vect) { g_ms++; }

void blink(void) {
  gpio_write(LED6_PIN, 1);
  for (volatile uint32_t i = 0; i < 60000UL; i++) {
  }
  gpio_write(LED6_PIN, 0);
  for (volatile uint16_t i = 0; i < 30000UL; i++) {
  }
}

void on_speed(void) {
  buzzer_start(1, BUZZER_SHORT_MS, BUZZER_GAP_MS);
  set_speed(next_speed(g_speed));
}

void turn_off(void) {
  if (g_speed != SPEED_OFF) {

    buzzer_start(2, BUZZER_LONG_MS, BUZZER_GAP_MS);
    set_speed(SPEED_OFF);
  }
  g_timer_sel_hours = 0;
  g_timer_seconds_remaining = 0;
  update_leds();
}

int main(void) {
  io_init();
  timer0_init();
  ir_init();
  blink();
  sei();

  debounce_t on_db = {0, false};
  debounce_t off_db = {0, false};

  uint32_t last_debounce_ms = 0;
  uint32_t last_second_ms = 0;

  for (;;) {
    uint32_t now_ms;
    cli();
    now_ms = g_ms;
    sei();

    buzzer_update(now_ms);

    if ((uint32_t)(now_ms - last_debounce_ms) >= 10) {
      last_debounce_ms += 10;

      bool on_raw = (gpio_read(ON_KEY_PIN) == 0);
      bool off_raw = (gpio_read(OFF_KEY_PIN) == 0);

      if (debounce_update(&on_db, on_raw)) {
        on_speed();
      }

      if (debounce_update(&off_db, off_raw)) {
        turn_off();
      }
    }

    uint8_t cmd;
    if (ir_take_command(&cmd)) {
      switch (cmd) {
      case IR_CMD_ON:
        on_speed();
        break;
      case IR_CMD_OFF:
        turn_off();
        break;
      case IR_CMD_TIME:
        if (g_speed != SPEED_OFF)
          rotate_timer();
      }
    }

    if ((uint32_t)(now_ms - last_second_ms) >= 1000) {
      last_second_ms += 1000;
      if (g_timer_seconds_remaining > 0 && g_speed != SPEED_OFF) {
        g_timer_seconds_remaining--;
        if (g_timer_seconds_remaining == 0) {
          g_timer_sel_hours = 0;
          set_speed(SPEED_OFF);
          buzzer_start(1, BUZZER_LONG_MS, BUZZER_GAP_MS);
        }
        update_leds();
      }
    }
  }
}

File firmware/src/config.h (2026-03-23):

#ifndef CONFIG_H
#define CONFIG_H

#include "gpio.h"
#include <avr/io.h>
#include <stdint.h>

/*
 * Board configuration: signal mappings for ATmega328P
 *
 * - LEDs: PC0..PC5
 * - Buzzer: PD0
 * - IR: PD2 (INT0)
 * - Keys: PD3 (ON), PD4 (OFF)
 * - Relays: PD5 (LOW), PD6 (MID), PD7 (HIGH)
 */

#define LED1_PIN PIN_ENCODE(PORT_C, 0)
#define LED2_PIN PIN_ENCODE(PORT_C, 1)
#define LED3_PIN PIN_ENCODE(PORT_C, 2)
#define LED4_PIN PIN_ENCODE(PORT_C, 3)
#define LED5_PIN PIN_ENCODE(PORT_C, 4)
#define LED6_PIN PIN_ENCODE(PORT_C, 5)

#define BUZZER_PIN PIN_ENCODE(PORT_D, 0)
#define IR_PIN PIN_ENCODE(PORT_D, 2)
#define ON_KEY_PIN PIN_ENCODE(PORT_D, 3)
#define OFF_KEY_PIN PIN_ENCODE(PORT_D, 4)

#define RELAY_LOW_PIN PIN_ENCODE(PORT_D, 5)
#define RELAY_MID_PIN PIN_ENCODE(PORT_D, 6)
#define RELAY_HIGH_PIN PIN_ENCODE(PORT_D, 7)

#endif // CONFIG_H

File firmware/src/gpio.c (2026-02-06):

#include "gpio.h"
#include <avr/io.h>

void gpio_init(void) {}

void gpio_dir_set(uint8_t pin, uint8_t out) {
  uint8_t port = PIN_TO_PORT(pin);
  uint8_t bit = PIN_TO_BIT(pin);
  volatile uint8_t *ddr = PORT_TO_DDR(port);
  if (out)
    *ddr |= (1 << bit);
  else
    *ddr &= ~(1 << bit);
}

uint8_t gpio_pin_read(uint8_t pin) {
  uint8_t port = PIN_TO_PORT(pin);
  uint8_t bit = PIN_TO_BIT(pin);
  volatile uint8_t *pinreg = PORT_TO_PIN(port);
  return ((*pinreg) & (1 << bit)) ? 1 : 0;
}

void gpio_set_input(uint8_t pin, uint8_t pullup) {
  gpio_dir_set(pin, 0);
  gpio_pin_write(pin, pullup ? 1 : 0);
}

uint8_t gpio_read(uint8_t pin) { return gpio_pin_read(pin); }

void gpio_pin_write(uint8_t pin, uint8_t v) {
  uint8_t port = PIN_TO_PORT(pin);
  uint8_t bit = PIN_TO_BIT(pin);
  volatile uint8_t *portreg = PORT_TO_REG(port);
  if (v)
    *portreg |= (1 << bit);
  else
    *portreg &= ~(1 << bit);
}

void gpio_set_output(uint8_t pin) { gpio_dir_set(pin, 1); }

void gpio_write(uint8_t pin, uint8_t v) { gpio_pin_write(pin, v); }

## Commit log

2026-02-06 "final" touches on v1 board
    [ac400.csv, ac400.kicad_pcb, ac400.kicad_sch]
2026-02-08 mounting holes distance and library references fix
    [ac400.kicad_pcb, ac400.kicad_sch]
2026-02-08 LED divider grid
    [ac400board-divider.3mf, ac400board.FCStd]
2026-02-19 generate / render files from kicad
    [ac400.kicad_pcb, ac400.kicad_sch]
2026-03-05 Exclude non-component items from BOM
    [ac400.csv, ac400.kicad_sch]
2026-03-07 Replace MCU, fix SPI pins and footprint
    [ac400.kicad_pcb, ac400.kicad_sch]
2026-03-07 update docs with schematic changes
2026-03-07 add box model, slightly shifted rail for divider
    rail had to be moved away, it wouldn't fit next to the switch.
    [ac400board-box.3mf, ac400board-divider.3mf, ac400board.FCStd]
2026-03-22 fw is good, but IR has issues
    [main.c]
2026-03-23 update design to KiCad 10.0 version
    [ac400.kicad_pcb, ac400.kicad_sch]
2026-04-03 update kicad model to 10
    [ac400.kicad_pcb]
2026-04-03 button shield and extender, better measurements
    [ac400board.FCStd]
2026-04-03 update 3d models
    [ac400board-button.3mf, ac400board-divider.3mf, ac400board-switch-stabilizer.3mf]
